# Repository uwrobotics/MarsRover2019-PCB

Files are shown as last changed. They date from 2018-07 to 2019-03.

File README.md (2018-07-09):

# MarsRover2019-PCB
Contains schematics and PCB designs

Conflict Resolution
If you're updating a library or any binary file, and git tells you there is a conflict, please follow the following steps to resolve it:
1. Copy your local version somewhere else (ex. desktop).
2. Undo your changes.
3. Pull all the changes from the repository, overwriting your local copy.
4. Make your changes in the updated version of the file.
5. Commit and push your changes.

If you made a lot of changes, or you suspect someone else is working on the same file as you at the same time, then you can check the change log on github.com, the app, or the terminal (git log) to see who made the most recent changes to the file.

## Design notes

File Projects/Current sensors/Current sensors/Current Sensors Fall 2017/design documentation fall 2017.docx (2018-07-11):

Current Sensor Boards Fall 2017 Design

Overview:

Boards are set up for 3v3 supply voltage.

Sensors are bidirectional and normally output 2.5V <Vout < 4.5V on their respective ranges (20A or 30A). But since a 3v3 supply is used the range is 1.65 <Vout< 2.97 for the full 0-20A range or 0-30A range. For the 5A board, a 20A sensor is being used so the range is 1.65<Vout< 1.98. This voltage range is being mapped onto as close to [0,3.3] as possible to get maximum resolution.

Using a 20A hall-effect sensor to sense current both on 20A and 5A range. Using a 30A hall-effect sensor to sense current on a 30A range. These boards have been tested. Resistor values and current vs voltage from op-amp data is contained in the “20A and 30A board new resistors oct 31 3v3” document.

In progress:

As of November 11 2017:

ADCs have not been ordered. 100A board has not been tested.

The ADCs originally planned for do not have selectable I2C addresses. This is an issue because 6 boards are needed for motors, 1 board for the battery, and one board for the end-effector. To address this problem there are 5 courses of action that can be taken (2, 4 and 5 are most promising because we can buy $1.2 single address ADCs)

1. Purchase eight 5-7$ ADCs with 3 address pins, respin boards
2. Purchase ADA fruit i2c expander break-out (MUX) and run clock and data lines to the break-out then a single SDA and SCL to the arb board
  a. Need a good way of connecting the lines to the breakout
    i. pin headers and solder wires and use wire-wire connectors?
3. Purchase eight 4$ ADCs with 4 selectable addresses and use a transistor to multiplex
4. Buy a $0.60 8:1 multiplexer IC and incorporate it into the arm board. This would mean that connectors would be needed for at least 6 clock and 6 data lines on the actual arm board.
5. Make a separate board for a multiplexer IC and the necessary connectors. Has the benefit of not having too many connectors on the actual arm board and also not having to elaborately find a way to get connectors on the adafruit break-out.

Robert Toyonaga fall 2017

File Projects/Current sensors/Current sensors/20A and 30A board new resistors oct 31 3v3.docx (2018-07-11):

Current | Voltage from op amp (1) | (2) | (3)
0 | 2.36 | 2.406 | 3.278
0.5 | 2.33 | 2.371 | 3.207
1 | 2.30 | 2.340 | 3.138
1.5 | 2.29 | 2.321 | 3.068
2 | 2.28 | 2.310 | 2.999
2.5 | 2.27 | 2.305 | 2.929
3 | | 2.302 | 2.859
3.5 | | | 2.790
4 | | | 2.720
4.5 | | | 2.650
5 | | | 2.581

3v3 20A board

After trial 2. I re-soldered on the op amp. Realized one pad needed more solder. Worked fine afterwards.

3v3 30A board

Current

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
Current | Voltage from op-amp
0 | 3.207
0.5 | 3.161
1 | 3.116
1.5 | 3.071
2 | 3.026
2.5 | 2.981
3 | 2.935
3.5 | 2.890
4 | 2.844
4.5 | 2.797
5 | 2.752

Had issues getting power supply leads to work. Tested with multimeter got 1<r<1Mohm

Make sure banana plugs are in securely sometimes I had to wiggle them in.

Current | Voltage from op-amp
0 | 3.207
0.5 | 3.161
1 | 3.116
1.5 | 3.071
2 | 3.026
2.5 | 2.981
3 | 2.935
3.5 | 2.890
4 | 2.844
4.5 | 2.797
5 | 2.752

3v3 5A

Current | Voltage from op-amp | R68= 39 R21 = 4.7
0 | 3.298 | 3.228
0.5 | 3.195 | 2.946
1 | 2.882 | 2.684
1.5 | 2.569 | 2.422
2 | 2.255 | 2.162
2.5 | 1.948 | 1.903
3 | 1.644 | 1.643
3.5 | 1.334 | 1.385
4 | 1.025 | 1.126
4.5 | 0.714 | 0.865
5 | 0.380 | 0.606

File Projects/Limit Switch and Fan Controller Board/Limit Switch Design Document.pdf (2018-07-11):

# Limit Switch Board Document

## 1 Introduction

This brief document provides a general overview of the Limit Switch Board (or Limits Board), designed for the University of Waterloo Robotics Team (Mars Rover 2018) by Josh Rubin. The schematic and layout for this board can be found on the UW Robotics GrabCad, or the reader can contact the designer to obtain the files if necessary. The reader can contact the board designer at josh.rubin@edu.uwaterloo.ca.

The board serves two major purposes on the UW Mars Rover: it acts as a hardware solution to monitor and control the mechanical limits of the rover’s arm, and to automatically control a fan based on the ambient temperature.

## 2 The Board

The board consists of two major circuits; the limit switch combinational logic, and the temperature dependant fan controller. Each of these circuits will now be discussed in further detail.

### 2.1 Limit Switch Combinational Logic

This section of the board deals with handling the mechanical limits of the rover’s arm. At a high level, the circuit cuts the PWM that is delivered to a motor controller when a limit switch has been triggered and the microcontroller is still supplying the direction signal in the direction that is no longer physically allowed. If this is not the case, the circuit passes PWM to to a motor controller. The circuit does not simply break the PWM indefinitely. If the opposite direction is provided by the controller, the PWM signal will be allowed to pass again, and once the arm reaches a location where the limit switch is no longer closed, the circuit will go back to its original state. The circuit’s operation is clearly explained by an example in Section 2.1.1.

The circuit for 1 motor with bidirectional limiting (mechanical limits on two directions of motion; say, arm moving right and arm moving left) consists of 2 Single Pole Double Throw (SPDT) limit switches, a 2 input XOR gate, and a 2:1 multiplexer (MUX), and connections to HIGH (3.3V), LOW (GND) and associated pull-up and pull-down resistors.

Figure 1 below illustrates a high level (block diagram) of the circuit. The box on the left represents the microcontroller (located on the Arm Board) providing the direction and PWM signals to the motors, the middle block is the combinational logic, and the right block represents the output direction and PWM being fed to the motor drivers.

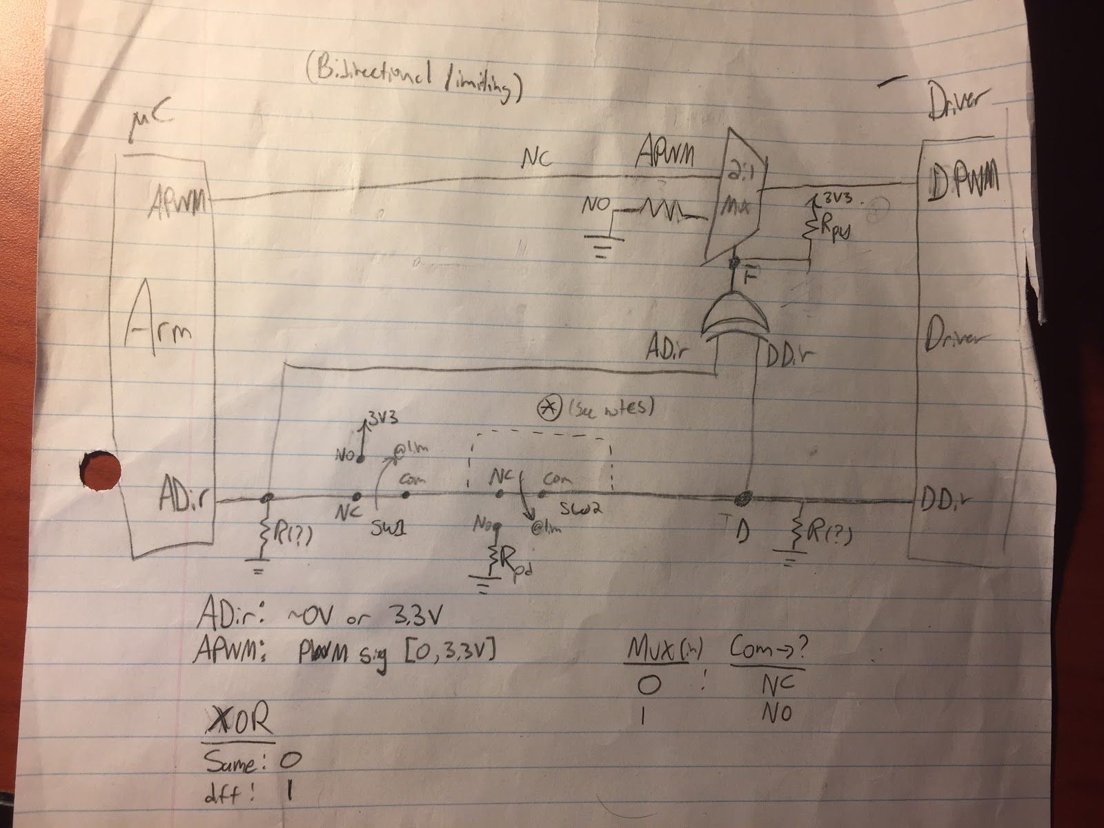
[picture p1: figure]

Figure 1. A block diagram of the limit switch combinational logic.

The operation of the circuit is best described through the use of an example.

2.1.1 Example of Operation
The limit switches are connected so that the direction input is the same as the direction output when a limit has not been reached (ADir = DDir). If one of the limits is reached, the limit switch then switches to the NO position, which is tied to either HIGH or LOW. Since the direction signal is either HIGH (defined as RIGHT for example) or LOW (defined as LEFT for example), this essentially asserts a direction on the motor controller. That is, when a limit switch is triggered, the circuit asserts the opposite direction (i.e., the direction the arm is allowed to move in) on the motor. The next paragraph discusses the PWM, which controls whether or not the motor is moving.

The XOR logic (LOW if the inputs are the same, HIGH if they are different) outputs the digital HIGH/LOW input of the selector on the MUX. If the two direction signals are the same, then the PWM signal will be selected by the MUX (NC signal). If the direction signals are different as is the case when a limit switch has been hit, GND (0 PWM) will be selected by the MUX. That means that when a limit switch has been triggered, the circuit will disable the PWM, and thus stop the motor from moving. The next paragraph discusses how the motor can move in the opposite direction again after a limit has been reached.

The circuit does not prevent the motor from moving indefinitely. If the microcontroller provides the same direction as the one being asserted by the limit switch (that is, the direction of valid motion), then the two direction inputs become the same and thus the XOR logic will ensure that PWM is selected. The reason this is possible is because the ADir and DDir line (seen in Figure
1) is essentially broken into two when a limit is reached. Thus, when a limit is reached, ADir and DDir become different lines, and are therefore independent. This is one of the reasons the logic works in the first place. Once the arm moves such that the limit switch is no longer closed, the circuit goes back to its original state. This logic therefore prevents the motor from being stuck indefinitely.

2.1.2 Notes
1. Shorting one of the limit switches in the circuit causes the limiting to become unidirectional (the operation is the same, except only one direction can be tracked and asserted).
2. The “R(?)” pull-down resistors in Figure 1 are implemented in the final design as pull-down resistors to ensure default logic values at the XOR gates.
3. Additionally, the pull-up resistor (versus pull-down) are used between the XOR and MUX since the sourced XOR uses an Open Collector Output.
4. The D and F markers on Figure 1 (near DDir and the output of the XOR gate) are two signals that are provided to the board’s microcontroller to indicate whether or not a limit has been reached (F) and which direction is currently being asserted by the circuit (D). Note that F could possibly be LOW (not asserted) even if one of the limits is switched. This would only be for the brief period of time between when the motor is moving in the correct direction but the limit switch is still triggered. That being said, if the limit switch is still activated and the controller again provides the invalid direction, the circuit will again cut the PWM since the XOR output will become HIGH once again. This edge case should not impact the operation or correctness of the monitoring.

2.1.3 Sourced Logic Components
2:1 MUX: http://www.ti.com/lit/ds/symlink/ts3a24159.pdf
XOR: http://www.ti.com/lit/ds/symlink/sn74lvc2g86.pdf

### 2.2 Fan Controller

The fan circuit uses the Microchip TC648 Fan Controller. This controller provides a PWM signal to control the speed of a fan depending on the output from a simple temperature sensor circuit.

Depending on the choice of thermistor and resistor values in the temperature circuit, the designer can adjust the temperature range in which the fan will operate, and that PWM will be supplied to the fan within that range. For example, in the originally designed circuit for this board, the fan will run at 50% PWM at 30 degrees, 100% PWM above 50 degrees, and have a roughly linear increase in PWM over that temperature range. The fan will also automatically shut off when the temperature is below 30 degrees (based on the output of a simple voltage divider circuit).

The circuit is essentially the same as the one shown in the device datasheet. The datasheet can be found here: http://ww1.microchip.com/downloads/en/DeviceDoc/21448D.pdf.

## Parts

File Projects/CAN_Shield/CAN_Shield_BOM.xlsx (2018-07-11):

CAN Shield BOM
Part | Quantity | Description | Link | Cost
CAN Transceiver | 1 | TJA1051T/3.118 | https://www.digikey.com/product-detail/en/nxp-usa-inc/TJA1051T-3118/568-8684-1-ND/2803570 | 1.36
Resistor | 2 | 120Ohm SMD 0805 | https://www.digikey.ca/product-detail/en/stackpole-electronics-inc/RMCF0805JT120R/RMCF0805JT120RCT-ND/1942540 | 0.28
Header Pin | 6 | Link gives 3 header pins per unit | https://www.digikey.ca/product-detail/en/wurth-electronics-inc/61300311121/732-5316-ND/4846825 | 0.34
JST Connector | 2 | 3 pin | Not sure where we sourced them last time
 |  |  |  | 1.98

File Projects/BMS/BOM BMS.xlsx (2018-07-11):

quantity | digikey part number | customer reference
1 | DMP2035U-7DICT-ND | (BMS) p chan mosfet
4 | SDM2U40CSP-7BDICT-ND | (BMS) diodes
1 | RR08P8.2KDTR-ND | 8.2k resistors
1 | RR08P2.7KDTR-ND | 2.7k resistors
1 | WM17469-ND | ribbon

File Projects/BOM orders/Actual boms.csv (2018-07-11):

Index | Quantity | Part Number | Manufacturer Part Number | Description | Customer Reference | Backorder | Unit Price | Extended Price
1 | 30 | 490-4781-1-ND | GCM188R72A103KA37D | CAP CER 10000PF 100V X7R 0603 | 10NF | 0 | 0.06800 | $2.04
2 | 30 | 490-9654-1-ND | GRM188R61E104KA01D | CAP CER 0.1UF 25V X5R 0603 | 0.1 UF | 0 | 0.13600 | $4.08
3 | 30 | 490-3298-1-ND | GRM188R60G106ME47D | CAP CER 10UF 4V X5R 0603 | 10UF | 0 | 0.17300 | $5.19
4 | 30 | 478-1215-1-ND | 06035C102KAT2A | CAP CER 1000PF 50V X7R 0603 | 1NF | 0 | 0.07800 | $2.34
5 | 30 | 455-1819-ND | B04B-PASK(LF)(SN) | CONN HEADER PA 4POS TOP 2MM TIN | PWR AND I2C CONN 180 TH | 0 | 0.44400 | $13.32
6 | 30 | 455-1488-ND | PAP-04V-S | CONN HOUSING PA 4POS 2MM WHITE | HOUSINGS PWR AND I2C | 0 | 0.16640 | $4.99
7 | 60 | 455-1325-1-ND | SPHD-001T-P0.5 | CONN TERM PHD CRIMP 22-26AWG TIN | CRIMPS PWR AND I2C | 0 | 0.04980 | $2.99
8 | 10 | MCP6001T-I/OTCT-ND | MCP6001T-I/OT | IC OPAMP GP 1MHZ RRO SOT23-5 | OP AMP | 0 | 0.37000 | $3.70
9 | 30 | RNCF0805DTE10K0CT-ND | RNCF0805DTE10K0 | RES 10K OHM 0.5% 1/8W 0805 | RES SMD 10K OHM 0.5% 1/8W 0805 | 0 | 0.20800 | $6.24
10 | 30 | P18KDACT-ND | ERA-6AEB183V | RES SMD 18K OHM 0.1% 1/8W 0805 | RES SMD 18K OHM 0.1% 1/8W 0805 | 0 | 0.44800 | $13.44
11 | 30 | P22KDACT-ND | ERA-6AEB223V | RES SMD 22K OHM 0.1% 1/8W 0805 | RES SMD 22K OHM 0.1% 1/8W 0805 | 0 | 0.44800 | $13.44
12 | 10 | 620-1191-1-ND | ACS712ELCTR-30A-T | SENSOR CURRENT HALL 30A AC/DC | 30A SENSOR | 0 | 5.85300 | $58.53
13 | 10 | ADC081C021CIMM/NOPBCT-ND | ADC081C021CIMM/NOPB | IC ADC 8BIT I2C 188KSPS 8VSSOP | IC ADC 8BIT I2C 188KSPS 8VSSOP | 0 | 2.20900 | $22.09
14 | 10 | ED2677-ND | OSTT7022150 | TERMINAL BLOCK 9.52MM 2POS PCB | SCREW TERMS | 0 | 1.48000 | $14.80
15 | 20 | 445-8018-1-ND | C1005X5R1E334K050BB | CAP CER 0.33UF 25V X5R 0402 | 0.33UF | 0 | 0.18500 | $3.70
16 | 20 | 490-3298-1-ND | GRM188R60G106ME47D | CAP CER 10UF 4V X5R 0603 | 10UF | 0 | 0.17300 | $3.46
17 | 40 | 490-3117-1-ND | GJM1555C1H150JB01D | CAP CER 15PF 50V C0G/NP0 0402 | 15 PF | 0 | 0.22000 | $8.80
18 | 20 | 311-1372-1-ND | CC0603ZRY5V7BB105 | CAP CER 1UF 16V Y5V 0603 | 1UF | 0 | 0.08600 | $1.72
19 | 30 | 455-1578-1-ND | BM02B-GHS-TBT(LF)(SN)(N) | CONN HEADER GH TOP 2POS 1.25MM | GH 2 | 0 | 0.56400 | $16.92
20 | 20 | 455-1579-1-ND | BM03B-GHS-TBT(LF)(SN)(N) | CONN HEADER GH TOP 3POS 1.25MM | GH 3 | 0 | 0.62800 | $12.56
21 | 30 | 455-1580-1-ND | BM04B-GHS-TBT(LF)(SN)(N) | CONN HEADER GH TOP 4POS 1.25MM | GH4 | 0 | 0.57500 | $17.25
22 | 30 | 455-1581-1-ND | BM05B-GHS-TBT(LF)(SN)(N) | CONN HEADER GH TOP 5POS 1.25MM | GH 5 | 0 | 0.60100 | $18.03
23 | 10 | 1253-1730-1-ND | CX2520DB32000D0GPSC1 | CRYSTAL 32.0000MHZ 8PF SMD | CRYSTAL | 0 | 0.88100 | $8.81
24 | 10 | MC33269DT-3.3GOS-ND | MC33269DT-3.3G | IC REG LINEAR 3.3V 800MA DPAK-3 | LDO | 0 | 0.95200 | $9.52
25 | 7 | LTC2875HS8#PBF-ND | LTC2875HS8#PBF | IC TXRX CAN 4MBPS 8SO | TRANCEIVER | 7 | 6.39000 | $44.73
26 | 20 | 1642-1324-1-ND | LS75C4D-T | SWITCH TACT SPST-NO 0.02A 12V | BUTTON PWR | 0 | 0.55700 | $11.14
27 | 20 | CKN10777CT-ND | KXT 311 LHS | SWITCH TACTILE SPST-NO 0.02A 15V | BUTTON SIGNAL | 0 | 0.35400 | $7.08
28 | 20 | 311-120GRCT-ND | RC0603JR-07120RL | RES SMD 120 OHM 5% 1/10W 0603 | 120 R | 0 | 0.01600 | $0.32
29 | 10 | 497-15167-ND | STM32F091RCT6 | IC MCU 32BIT 256KB FLASH 64LQFP | STM32F091RC | 0 | 5.94900 | $59.49
30 | 10 | 1727-1306-1-ND | PESD1CAN-UX | TVS DIODE 24V 50V SOT323-3 | CAN DIODE | 0 | 0.43200 | $4.32
31 | 15 | PCE4549CT-ND | EEE-FPV100UAR | CAP ALUM 10UF 20% 35V SMD | 10 UF POLARIZED | 0 | 0.50400 | $7.56
32 | 2 | VEML7700CT-ND | VEML7700-TR | IC AMBIENT LIGHT SENSOR I2C SMT | LIGHT SENSOR | 0 | 2.88000 | $5.76
33 | 10 | 455-1833-ND | B03B-PASK-1(LF)(SN) | CONN HEADER PA 3POS TOP W/BOSS | PA 3 | 0 | 0.37200 | $3.72
34 | 5 | DMP2035U-7DICT-ND | DMP2035U-7 | MOSFET P-CH 20V 3.6A SOT-23 | (BMS) P CHAN MOSFET | 0 | 0.78000 | $3.90
35 | 10 | SDM2U40CSP-7BDICT-ND | SDM2U40CSP-7B | DIODE SCHOTTKY 40V 2A X3-WLB1608 | (BMS) DIODES | 0 | 0.48200 | $4.82
36 | 10 | P8.2KDBCT-ND | ERA-3AEB822V | RES SMD 8.2K OHM 0.1% 1/10W 0603 | 8.2K RESISTORS | 0 | 0.44500 | $4.45
37 | 10 | RR08P2.7KDCT-ND | RR0816P-272-D | RES SMD 2.7K OHM 0.5% 1/16W 0603 | 2.7K RESISTORS | 0 | 0.14500 | $1.45
38 | 4 | WM17469-ND | 0878311420 | CONN HEADER 14POS 2MM VERT GOLD | RIBBON | 0 | 1.91000 | $7.64
39 | 1 | 455-1602-ND | GHR-12V-S | CONN GH HOUSING 12POS 1.25MM | 12 GH HOUSE | 0 | 0.28000 | $0.28
40 | 30 | 455-1594-ND | GHR-04V-S | CONN GH HOUSING 4POS 1.25MM | 4 GH HOUSE | 0 | 0.12920 | $3.88
41 | 10 | 455-1486-ND | PAP-02V-S | CONN HOUSING PA 2POS 2MM WHITE | 2 PA HOUSE | 0 | 0.19600 | $1.96
42 | 30 | 455-1595-ND | GHR-05V-S | CONN GH HOUSING 5POS 1.25MM | 5 GH HOUSE | 0 | 0.19040 | $5.71
43 | 50 | 455-1313-1-ND | SPHD-002T-P0.5 | CONN TERM PHD CRIMP 24-28AWG TIN | PA CRIMP | 0 | 0.04980 | $2.49
44 | 40 | 1276-1045-1-ND | CL10A475KQ8NNNC | CAP CER 4.7UF 6.3V X5R 0603 | 4.7 UF | 0 | 0.09600 | $3.84
45 | 20 | 475-1410-1-ND | LG R971-KN-1 | LED GREEN DIFFUSED 0805 SMD | GRN | 0 | 0.33400 | $6.68
46 | 20 | 475-1278-1-ND | LS R976-NR-1 | LED RED DIFFUSED 0805 SMD | RED | 0 | 0.35200 | $7.04
47 | 20 | 475-2560-1-ND | LY R976-PS-36 | LED YELLOW DIFFUSED 0805 SMD | YELLOW | 0 | 0.35200 | $7.04
48 | 40 | MCT0603-0.0-ZZCT-ND | MCT06030Z0000ZP500 | RES SMD 0 OHM JUMPER 1/8W 0603 | 0R | 0 | 0.25840 | $10.34
49 | 50 | RNCF0805DTE10K0CT-ND | RNCF0805DTE10K0 | RES 10K OHM 0.5% 1/8W 0805 | RES SMD 10K OHM 0.5% 1/8W 0805 | 0 | 0.20800 | $10.40
50 | 40 | 311-4.7KGRCT-ND | RC0603JR-074K7L | RES SMD 4.7K OHM 5% 1/10W 0603 | 4.7 K | 0 | 0.01600 | $0.64
51 | 20 | 455-1593-ND | GHR-03V-S | CONN GH HOUSING 3POS 1.25MM | 3 GH HOUSE | 0 | 0.16600 | $3.32
52 | 20 | 455-1487-ND | PAP-03V-S | CONN HOUSING PA 3POS 2MM WHITE | 3 PA HOUSE | 0 | 0.20500 | $4.10
 |  |  |  |  |  |  | Subtotal | $502.06

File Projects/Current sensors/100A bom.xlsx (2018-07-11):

quant | digikey pn | cust ref | board | link
1 | 490-4781-1-ND | 10nF | 100A
2 | 587-1245-1-ND | 0.1 uF | 100A
2 | 490-3298-1-ND | 10uf | 100A
1 | 478-1215-1-ND | 1nf | 100A
3 | 455-1819-ND | pwr and i2c conn 180 th | 100A
3 | 455-1488-ND | housings pwr and i2c | 100A
6 | 455-1325-1-ND | crimps pwr and i2c | 100A
1 | MCP6001T-I/OTCT-ND | op amp | 100A
2 | RNCF0805DTE10K0CT-ND | RES SMD 10K OHM 0.5% 1/8W 0805 | 100A
1 | P18KDACT-ND | RES SMD 18K OHM 0.1% 1/8W 0805 | 100A
1 | P22KDACT-ND | RES SMD 22K OHM 0.1% 1/8W 0805 | 100A
1 | 620-1465-5-ND | 100A sensor | 100A
1 | ADC081C021CIMM/NOPBCT-ND | IC ADC 8BIT I2C 188KSPS 8VSSOP | 100A

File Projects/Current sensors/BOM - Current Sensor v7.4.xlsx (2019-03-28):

RefDes | Value | Name | Part | Number of Pins | Pattern | Manufacturer | Manufacturer Part Number | Quantity | DigiKey Part Numbers | Datasheet
C1 | 1 nF | CAP_0805 | Part 1 | 2 | CAP_0805 | KEMET | C0402C102K5RACTU | 1 | 399-1032-2-ND (https://www.digikey.ca/product-detail/en/kemet/C0402C102K5RACTU/399-1032-2-ND/411034) | https://content.kemet.com/datasheets/KEM_C1002_X7R_SMD.pdf
C2 | 0.1 uF | CAP_0805 | Part 1 | 2 | CAP_0805 | KEMET | C0402C102K5RACTU | 1 | 399-1032-2-ND (https://www.digikey.ca/product-detail/en/kemet/C0402C102K5RACTU/399-1032-2-ND/411034) | https://content.kemet.com/datasheets/KEM_C1002_X7R_SMD.pdf
C3 | 10 uF | CAP_0805 | Part 1 | 2 | CAP_0805 | KEMET | C0402C102K5RACTU | 1 | 399-1032-2-ND (https://www.digikey.ca/product-detail/en/kemet/C0402C102K5RACTU/399-1032-2-ND/411034) | https://content.kemet.com/datasheets/KEM_C1002_X7R_SMD.pdf
C13 | 1 nF | CAP_0805 | Part 1 | 2 | CAP_0805 | KEMET | C0402C102K5RACTU | 1 | 399-1032-2-ND | https://content.kemet.com/datasheets/KEM_C1002_X7R_SMD.pdf
C14 | 10 uF | CAP_0805 | Part 1 | 2 | CAP_0805 | KEMET | C0402C102K5RACTU | 1 | 399-1032-2-ND | https://content.kemet.com/datasheets/KEM_C1002_X7R_SMD.pdf
C15 | 0.1 uF | CAP_0805 | Part 1 | 2 | CAP_0805 | KEMET | C0402C102K5RACTU | 1 | 399-1032-2-ND | https://content.kemet.com/datasheets/KEM_C1002_X7R_SMD.pdf
J1 |  | CON_2M_PH_TOP_SMT | Part 1 | 2 | JST-B2B-SM4-TB | Sponsored by JST | Sponsored by JST | 1 | Sponsored by JST | http://www.jst-mfg.com/product/pdf/eng/ePH.pdf
J4 |  | CON_4M_PH_TOP_SMT | Part 1 | 4 | JST-B4B-SM4-TB | Sponsored by JST | Sponsored by JST | 1 | Sponsored by JST | http://www.jst-mfg.com/product/pdf/eng/ePH.pdf
OPAMP |  | MCP6001(op amp) | Part 1 | 5 | MCP6001 | MICROCHIP | MCP6001RT-E/OT | 1 | MCP6001RT-E/OTCT-ND | http://ww1.microchip.com/downloads/en/DeviceDoc/21733j.pdf
R1 | 10K | RES | Part 1 | 2 | RES_0603 | Stackpole Electronics | RMCF0201FT10K0 | 1 | RMCF0201FT10K0TR-ND (https://www.digikey.com/product-detail/en/stackpole-electronics-inc/RMCF0201FT10K0/RMCF0201FT10K0TR-ND/1714990) | https://www.seielect.com/catalog/sei-rmcf_rmcp.pdf
R2 | 10K | RES | Part 1 | 2 | RES_0603 | Stackpole Electronics | RMCF0201FT10K0 | 1 | RMCF0201FT10K0TR-ND (https://www.digikey.com/product-detail/en/stackpole-electronics-inc/RMCF0201FT10K0/RMCF0201FT10K0TR-ND/1714990) | https://www.seielect.com/catalog/sei-rmcf_rmcp.pdf
R8 | 10K | RES | Part 1 | 2 | RES_0603 | Stackpole Electronics | RMCF0201FT10K0 | 1 | RMCF0201FT10K0TR-ND | https://www.seielect.com/catalog/sei-rmcf_rmcp.pdf
R9 | 10K | RES | Part 1 | 2 | RES_0603 | Stackpole Electronics | RMCF0201FT10K0 | 1 | RMCF0201FT10K0TR-ND | https://www.seielect.com/catalog/sei-rmcf_rmcp.pdf
R24 | 10K | RES_0805 | Part 1 | 2 | RES_0805 | Stackpole Electronics | RMCF0201FT10K0 | 1 | RMCF0201FT10K0TR-ND (https://www.digikey.com/product-detail/en/stackpole-electronics-inc/RMCF0201FT10K0/RMCF0201FT10K0TR-ND/1714990) | https://www.seielect.com/catalog/sei-rmcf_rmcp.pdf
R25 | 18K | RES_0805 | Part 1 | 2 | RES_0805 | Panasonic | ERA-3AEB183V | 1 | P18KDBTR-ND | https://industrial.panasonic.com/cdbs/www-data/pdf/RDM0000/AOA0000C307.pdf
R26 | 10K | RES_0805 | Part 1 | 2 | RES_0805 | Stackpole Electronics | RMCF0201FT10K0 | 1 | RMCF0201FT10K0TR-ND (https://www.digikey.com/product-detail/en/stackpole-electronics-inc/RMCF0201FT10K0/RMCF0201FT10K0TR-ND/1714990) | https://www.seielect.com/catalog/sei-rmcf_rmcp.pdf
R27 | 22K | RES_0805 | Part 1 | 2 | RES_0805 | Panasonic | ERA-3AEB223V | 1 | P22KDBTR-ND | https://industrial.panasonic.com/cdbs/www-data/pdf/RDM0000/AOA0000C307.pdf
sensor | 100A | ACS759 | Part 1 | 5 | ACS759 | Allegro Microsystems | ACS759LCB-100B-PFF-T | 1 | 620-1465-5-ND | www.allegromicro.com/~/media/Files/Datasheets/ACS759-Datasheet.ashx
U1 |  | ADC081C027 | Part 1 | 8 | IC ADC 8BIT I2C 188KSPS 8VSSOP | Texas Instruments | ADC081C027CIMKX/NOPB | 1 | ADC081C027CIMKX/NOPBTR-ND | http://www.ti.com/lit/ds/symlink/adc081c021.pdf
 |  |  |  | 52 |  |  |  | 19

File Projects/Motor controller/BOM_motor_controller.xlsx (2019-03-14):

Good? | Quantity | Name | Manufacturer | MPN | Price/unit | Total price | Digikey Link
Y | 3 | CAP_1uF_0603 | Yageo | CC0603ZRY5V7BB105 | 0.14 | 0.42 | https://www.digikey.ca/product-detail/en/yageo/CC0603ZRY5V7BB105/311-1372-1-ND/2103156
Y | 2 | CAP_0.1uF_0603 | Taiyo Yuden | GMK107B7104KAHT | 0.2 | 0.4 | https://www.digikey.ca/product-detail/en/taiyo-yuden/GMK107B7104KAHT/587-3354-1-ND/4157241
Y? | 1 | CAP_1000uF_POL | Illinois Capacitor | 108CKE050M | 1.23 | 1.23 | https://www.digikey.ca/products/en?keywords=108CKE050M
Y | 1 | CAP_10uF_2917 | Vishay Sprague | 293D106X0035D2TE3 | 0.9 | 0.9 | https://www.digikey.ca/product-detail/en/vishay-sprague/293D106X0035D2TE3/718-1046-1-ND/1559540
N | 1 | CAP_100nF_0603 | Yageo | CC0603KRX7R7BB104 | 0.14 | 0.14 | https://www.digikey.ca/product-detail/en/yageo/CC0603KRX7R7BB104/311-1088-1-ND/302998
N | 1 | BAS16GW | Nexperia | BAS16GW | 0.14 | 0.14 | https://www.digikey.ca/product-detail/en/nexperia-usa-inc/BAS16GWJ/1727-7320-1-ND/7390571
Y | 1 | DIO_LED_G | OSRAM | LG R971-KN-1 | 0.45 | 0.45 | https://www.digikey.ca/product-detail/en/osram-opto-semiconductors-inc/LG-R971-KN-1/475-1410-1-ND/1802598
Y | 1 | CON_3M_TH_180 | JST | JST-B03B-PASK | 0.38 | 0.38 | https://www.digikey.ca/product-detail/en/jst-sales-america-inc/B03B-PASK-1-LF-SN/455-1833-ND/926739
Y | 1 | Female for CON_3M_TH_180 | JST | PAP-03V-S | 0.22 | 0.22 | https://www.digikey.ca/product-detail/en/jst-sales-america-inc/PAP-03V-S/455-1487-ND/759975
Y | 2 | CON_2M_30A | On Shore Technology Inc | OSTYK51102030 | 1.37 | 2.74 | https://www.digikey.ca/product-detail/en/on-shore-technology-inc/OSTYK51102030/ED2953-ND/1588818
Y | 5 | NMOS_40V_75A | Nexperia | BUK765R3-40E | 1.46 | 7.3 | https://www.digikey.ca/product-detail/en/nexperia-usa-inc/BUK765R3-40E118/1727-7255-1-ND/3672520
Y? | 3 | NPN_40V_100mA | Micro Commercial Co | MMBT3904-TP | 0.14 | 0.42 | https://www.digikey.ca/product-detail/en/micro-commercial-co/MMBT3904-TP/MMBT3904TPMSCT-ND/717395
Y? | 1 | RES_43k_0603 | Yageo | RC0603JR-0743KL | 0.15 | 0.15 | https://www.digikey.ca/product-detail/en/yageo/RC0603JR-0743KL/311-43KGRCT-ND/729737
Y | 1 | RES_100R_0603 | Yageo | RC0603FR-07100RL | 0.15 | 0.15 | https://www.digikey.ca/product-detail/en/yageo/RC0603FR-07100RL/311-100HRCT-ND/729835
Y | 1 | RES_698k_0603 | Yageo | RC0603FR-07698KL | 0.15 | 0.15 | https://www.digikey.ca/product-detail/en/yageo/RC0603FR-07698KL/311-698KHRCT-ND/730309
Y? | 6 | RES_10K_0603 | Yageo | RC0603JR-0710KL | 0.15 | 0.9 | https://www.digikey.ca/product-detail/en/yageo/RC0603JR-0710KL/311-10KGRCT-ND/729647
Y | 2 | RES_150k_0603 | Yageo | RC0603JR-07150KL | 0.15 | 0.3 | https://www.digikey.ca/product-detail/en/yageo/RC0603JR-07150KL/311-150KGRCT-ND/729662
 | 2 | PUSHBUTTON_TACTILE | C&K | RS-282G05A3-SM RT | 1.15 | 2.3 | https://www.digikey.ca/product-detail/en/c-k/RS-282G05A3-SM-RT/CKN10384CT-ND/2747203
Y | 1 | DRV8701E | Texas Instruments | DRV8701ERGET | 4.12 | 4.12 | https://www.digikey.ca/product-detail/en/texas-instruments/DRV8701ERGET/296-42155-1-ND/5299196
Y | 1 | XOR_1 | ON Semiconductor | NC7SV86P5XCT-ND | 0.55 | 0.55 | https://www.digikey.ca/products/en?keywords=NC7SV86P5XCT-ND
Y | 1 | OSCILLATOR_2kHz | Microchip Technology | DSC6083CI2A-002K000 | 1.35 | 1.35 | https://www.digikey.ca/product-detail/en/microchip-technology/DSC6083CI2A-002K000/DSC6083CI2A-002K000-ND/6244496
 |  |  |  |  | Total | 23.13
 | 2 | SN74AHC1G02DBVT | Texas Instruments | SN74AHC1G02DBVT |  |  | https://www.digikey.ca/product-detail/en/texas-instruments/SN74AHC1G02DBVT/296-49867-1-ND/9462743
 | 2 | 74LVC1G3157GW,125 | Nexperia | 74LVC1G3157GW,125 |  |  | https://www.digikey.ca/product-detail/en/nexperia-usa-inc/74LVC1G3157GW125/1727-6073-1-ND/2753909

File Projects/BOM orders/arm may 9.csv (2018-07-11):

# | Quantity | MPN | Name | Value
17 | 1 | GRM188R71C334KA01D | CAP_0.33uF_0603 | 0.33uF
7 | 1 | CC0603KRX7R7BB104 | CAP_100nF_0603 | 100nF
8 | 1 | CC0603KRX7R7BB104 | CAP_100nF_0603 | 100nF
9 | 1 | CC0603KRX7R7BB104 | CAP_100nF_0603 | 100nF
10 | 1 | CC0603KRX7R7BB104 | CAP_100nF_0603 | 100nF
15 | 1 | CC0603KRX7R7BB104 | CAP_100nF_0603 | 100nF
16 | 1 | CC0603KRX7R7BB104 | CAP_100nF_0603 | 100nF
5 | 1 | CC0402KRX7R6BB103 | CAP_10nF_0603 | 10nF
12 | 1 |  | CAP_10uF_POL | 10uF
13 | 1 | GRM1555C1H150JA01D | CAP_15pF_0402 | 15pF
14 | 1 | GRM1555C1H150JA01D | CAP_15pF_0402 | 15pF
6 | 1 | CC0603ZRY5V7BB105 | CAP_1uF_0603 | 1uF
11 | 1 | CC0603KRX5R5BB475 | CAP_4.7uF_0603 | 4.7uF
18 | 1 | CC0603KRX5R5BB475 | CAP_4.7uF_0603 | 4.7uF
29 | 1 |  | CON _12M_SM_180
44 | 1 |  | CON_2M_SM_180
43 | 1 |  | CON_2M_TH_180
31 | 1 |  | CON_3M_SM_180
32 | 1 |  | CON_3M_SM_180
33 | 1 |  | CON_3M_SM_180
39 | 1 |  | CON_3M_SM_180
41 | 1 |  | CON_3M_SM_180
45 | 1 |  | CON_3M_SM_180
30 | 1 |  | CON_4M_SM_180
36 | 1 |  | CON_4M_SM_180
37 | 1 |  | CON_4M_SM_180
38 | 1 |  | CON_4M_SM_180
34 | 1 |  | CON_5M_SM_180
35 | 1 |  | CON_5M_SM_180
40 | 1 |  | CON_5M_SM_180
42 | 1 |  | CON_5M_SM_180
73 | 1 |  | CRYSTAL | 8MHz
22 | 1 | LG R971-KN-1 | DIO_LED_G | GREEN
23 | 1 | LG R971-KN-1 | DIO_LED_G | GREEN
24 | 1 | LG R971-KN-1 | DIO_LED_G | GREEN
26 | 1 | LS R976-NR-1 | DIO_LED_R | RED
25 | 1 | LY R976-PS-36 | DIO_LED_Y | YELLOW
69 | 1 | MC33269DT-3.3 | LDO_3V3_DPAK
68 | 1 |  | LTC2875 | IC TXRX CAN
64 | 1 | FSM2JSMAA | PUSHBUTTON_PWR
3 | 1 | KXT 311 LHS | PUSHBUTTON_SIGNAL
4 | 1 | KXT 311 LHS | PUSHBUTTON_SIGNAL
59 | 1 | RC0603JR-070RL | RES_0R_0603 | 0R
61 | 1 | RC0603JR-070RL | RES_0R_0603 | 0R
55 | 1 | RC0603FR-07100RL | RES_100R_0603 | 100R
56 | 1 | RC0603FR-07100RL | RES_100R_0603 | 100R
57 | 1 | RC0603FR-07100RL | RES_100R_0603 | 100R
58 | 1 | RC0603FR-07100RL | RES_100R_0603 | 100R
62 | 1 | RC0603FR-07100RL | RES_100R_0603 | 100R
46 | 1 | RC0603JR-0710KL | RES_10K_0603 | 10K
47 | 1 | RC0603JR-0710KL | RES_10K_0603 | 10K
48 | 1 | RC0603JR-0710KL | RES_10K_0603 | 10K
49 | 1 | RC0603JR-0710KL | RES_10K_0603 | 10K
50 | 1 | RC0603JR-0710KL | RES_10K_0603 | 10K
51 | 1 | RC0603JR-0710KL | RES_10K_0603 | 10K
52 | 1 | RC0603JR-0710KL | RES_10K_0603 | 10K
63 | 1 | RC0603JR-0710KL | RES_10K_0603 | 10K
60 | 1 | RC0603JR-07120RL | RES_120R_0603 | 120R
53 | 1 | RC0603JR-074K7L | RES_4.7K_0603 | 4.7K
54 | 1 | RC0603JR-074K7L | RES_4.7K_0603 | 4.7K
67 | 1 |  | STM32F091RC
1 | 1 |  | TESTPOINT
2 | 1 |  | TESTPOINT
19 | 1 |  | TESTPOINT
20 | 1 |  | TESTPOINT
27 | 1 |  | TESTPOINT
28 | 1 |  | TESTPOINT
65 | 1 |  | TESTPOINT
66 | 1 |  | TESTPOINT
70 | 1 |  | TESTPOINT
71 | 1 |  | TESTPOINT
72 | 1 |  | TESTPOINT
21 | 1 | PESD1CAN-UX | TVS_DIODE_CAN
 | 73

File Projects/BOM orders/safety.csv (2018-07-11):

# | Quantity | MPN | Name | Value
1 | 1 |  | TESTPOINT
2 | 1 |  | TESTPOINT
3 | 1 |  | TESTPOINT
4 | 1 |  | JST-B02B-PASK
5 | 1 | RC0603JR-070RL | RES_0R_0603 | 0R
6 | 1 |  | TESTPOINT
7 | 1 |  | JST-B02B-PASK
8 | 1 |  | TESTPOINT
9 | 1 | RC0603JR-070RL | RES_0R_0603 | 0R
10 | 1 |  | JST-B02B-PASK
11 | 1 | RC0603JR-070RL | RES_0R_0603 | 0R
12 | 1 |  | TESTPOINT
13 | 1 |  | JST-B02B-PASK
14 | 1 | KXT 311 LHS | PUSHBUTTON_SIGNAL
15 | 1 | KXT 311 LHS | PUSHBUTTON_SIGNAL
16 | 1 |  | TESTPOINT
17 | 1 |  | TESTPOINT
18 | 1 | GRM1555C1H150JA01D | CAP_15pF_0402 | 15pF
19 | 1 | GRM1555C1H150JA01D | CAP_15pF_0402 | 15pF
20 | 1 | CC0603KRX7R7BB104 | CAP_100nF_0603 | 100nF
21 | 1 | CC0603KRX7R7BB104 | CAP_100nF_0603 | 100nF
22 | 1 | CC0603KRX7R7BB104 | CAP_100nF_0603 | 100nF
23 | 1 | CC0603KRX7R7BB104 | CAP_100nF_0603 | 100nF
24 | 1 | CC0603KRX5R5BB475 | CAP_4.7uF_0603 | 4.7uF
25 | 1 | CC0603KRX7R7BB104 | CAP_100nF_0603 | 100nF
26 | 1 | CC0603KRX5R5BB475 | CAP_4.7uF_0603 | 4.7uF
27 | 1 | CC0402KRX7R6BB103 | CAP_10nF_0603 | 10nF
28 | 1 | CC0603ZRY5V7BB105 | CAP_1uF_0603 | 1uF
29 | 1 | GRM188R71C334KA01D | CAP_0.33uF_0603 | 0.33uF
30 | 1 |  | CAP_10uF_POL | 10uF
31 | 1 | CC0603KRX7R7BB104 | CAP_100nF_0603 | 100nF
32 | 1 | 860020672011 | CAP_22uF_POL | 10uF
33 | 1 | CC0603KRX7R7BB104 | CAP_100nF_0603 | 100nF
34 | 1 | 860020672011 | CAP_22uF_POL | 10uF
35 | 1 | CC0603KRX7R7BB104 | CAP_100nF_0603 | 100nF
36 | 1 |  | TESTPOINT
37 | 1 |  | TESTPOINT
38 | 1 | CC0402KRX7R6BB103 | CAP_10nF_0603 | 10nF
39 | 1 | CC0402KRX7R6BB103 | CAP_10nF_0603 | 10nF
40 | 1 | CC0603ZRY5V7BB105 | CAP_1uF_0603 | 1uF
41 | 1 | CC0603ZRY5V7BB105 | CAP_1uF_0603 | 1uF
42 | 1 |  | DIO_SCHOTTKY
43 | 1 |  | DIO_SCHOTTKY
44 | 1 | LS R976-NR-1 | DIO_LED_R | RED
45 | 1 | LY R976-PS-36 | DIO_LED_Y | YELLOW
46 | 1 | LG R971-KN-1 | DIO_LED_G | GREEN
47 | 1 | PESD1CAN-UX | TVS_DIODE_CAN
48 | 1 | LG R971-KN-1 | DIO_LED_G | GREEN
49 | 1 | LG R971-KN-1 | DIO_LED_G | GREEN
50 | 1 |  | TESTPOINT
51 | 1 |  | TESTPOINT
52 | 1 |  | JST-B02B-PASK
53 | 1 |  | CON_4M_SM_180
54 | 1 |  | CON_4M_SM_180
55 | 1 |  | CON_3M_SM_180
56 | 1 |  | CON_5M_TH_180
57 | 1 |  | CON_4M_SM_180
58 | 1 |  | CON_3M_SM_180
59 | 1 |  | CON_5M_TH_180
60 | 1 |  | CON_3M_TH_180
61 | 1 |  | RES_THERMIS_NTC
62 | 1 |  | MOSFET_ENH_P
63 | 1 |  | MOSFET_ENH_N
64 | 1 |  | MOSFET_ENH_N
65 | 1 | AO3420 | NMOS_20V_6A
66 | 1 | RC0603JR-070RL | RES_0R_0603 | 0R
67 | 1 |  | RES_FIXED | 2.7k
68 | 1 |  | RES_FIXED | 8.2k
69 | 1 | RC0603FR-07100RL | RES_100R_0603 | 100R
70 | 1 | RC0603JR-0710KL | RES_10K_0603 | 10K
71 | 1 | RC0603JR-0710KL | RES_10K_0603 | 10K
72 | 1 | RC0603JR-074K7L | RES_4.7K_0603 | 4.7K
73 | 1 | RC0603JR-074K7L | RES_4.7K_0603 | 4.7K
74 | 1 | RC0603JR-0710KL | RES_10K_0603 | 10K
75 | 1 | RC0603JR-070RL | RES_0R_0603 | 0R
76 | 1 | RC0603FR-07100RL | RES_100R_0603 | 100R
77 | 1 | RC0603FR-07100RL | RES_100R_0603 | 100R
78 | 1 | RC0603JR-07120RL | RES_120R_0603 | 120R
79 | 1 | RC0603FR-07100RL | RES_100R_0603 | 100R
80 | 1 | RC0603FR-07100RL | RES_100R_0603 | 100R
81 | 1 | RC0603JR-0710KL | RES_10K_0603 | 10K
82 | 1 | RC0603JR-0710KL | RES_10K_0603 | 10K
83 | 1 |  | RES_FIXED | 10k
84 | 1 |  | RES_FIXED | 6.8k
85 | 1 |  | RES_FIXED | 6.8k
86 | 1 | RC0603JR-074K7L | RES_4.7K_0603 | 4.7K
87 | 1 | RC0603JR-074K7L | RES_4.7K_0603 | 4.7K
88 | 1 |  | RES_78.5k_0603 | 78.5k
89 | 1 |  | RES_85k_0603 | 85k
90 | 1 |  | RES_30.1k_0603 | 30.1k
91 | 1 |  | RES_20k_0603 | 20k
92 | 1 |  | RES_FIXED | 10k
93 | 1 |  | JST-B02B-PASK
94 | 1 |  | JST-B02B-PASK
95 | 1 |  | JST-B02B-PASK
96 | 1 |  | TESTPOINT
97 | 1 |  | TESTPOINT
98 | 1 |  | TESTPOINT
99 | 1 |  | TESTPOINT
100 | 1 | KXT 311 LHS | PUSHBUTTON_SIGNAL
101 | 1 |  | TESTPOINT
102 | 1 |  | TESTPOINT
103 | 1 |  | TESTPOINT
104 | 1 |  | STM32F091RC
105 | 1 | MC33269DT-3.3 | LDO_3V3_DPAK
106 | 1 |  | LTC2875 | IC TXRX CAN
107 | 1 |  | TC648B_OA
108 | 1 |  | CRYSTAL | 8MHz
 | 108

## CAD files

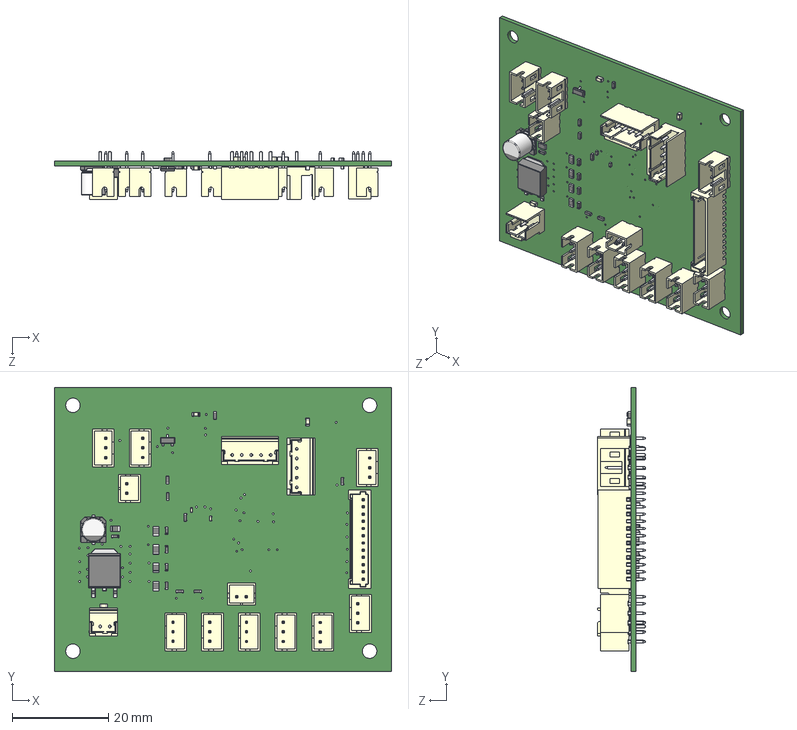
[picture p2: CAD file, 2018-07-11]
Projects/Arm board/armboard1_layout_12PINCONNECTOR.step
70.0 x 59.0 x 10.0 mm
Board
cap_0603 x 10
capae-5.3x5.3h6.1
cap_0402 x 2
sot23
res_0805 x 5
hdr-1x12tz_1.5_sh21x5
hdr-1x2t_2_sh6x5 x 2
hdr-1x3t_2_sh8x5 x 9
hdr-1x5t_2_sh12x6 x 2
hdr-1x2t_2_sh6x6
res_0603 x 18
to252-3(4)_10x6.6x2.28

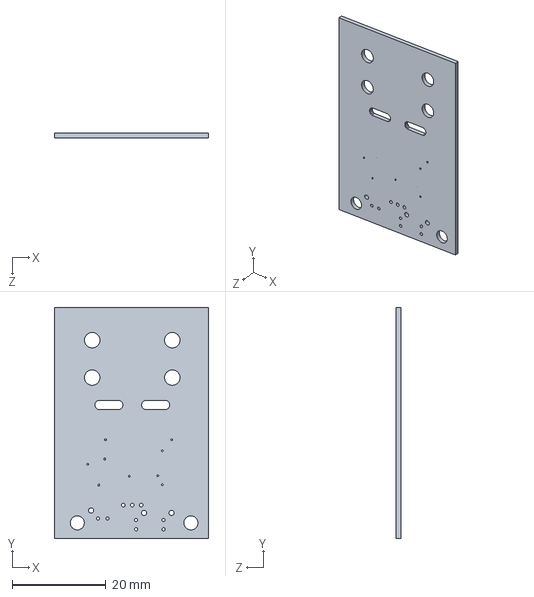
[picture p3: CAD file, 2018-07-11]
Projects/Current sensors/3d model.step
33.0 x 49.4 x 1.00 mm

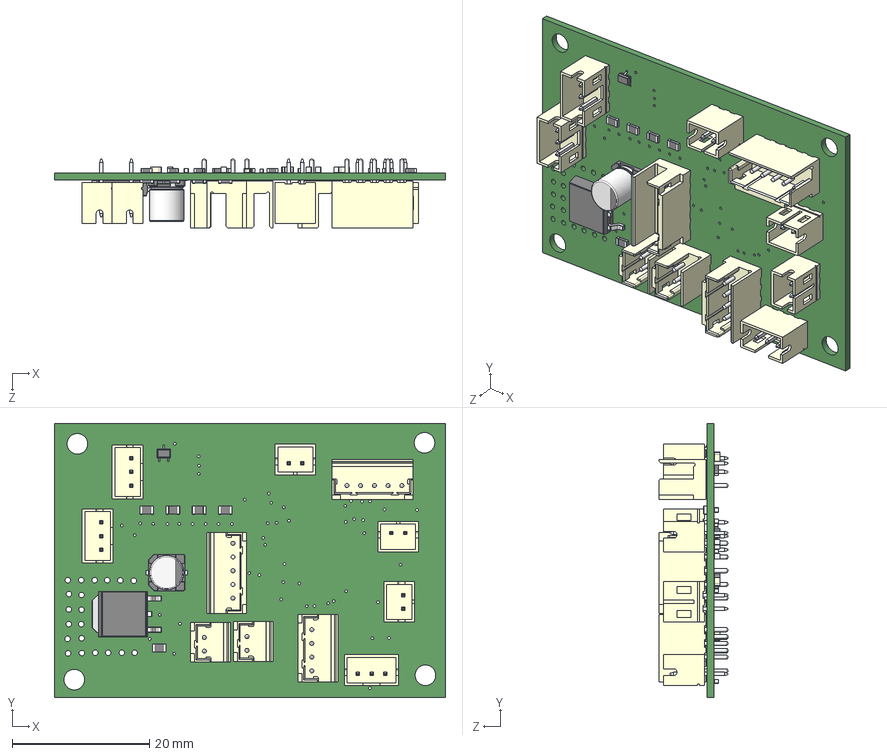
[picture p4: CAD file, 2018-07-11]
Projects/End effector/end_effector.step
57.0 x 40.0 x 10.0 mm
Board
cap_0402 x 2
cap_0603 x 11
capae-5.3x5.3h6.1
sot323
res_0805 x 5
hdr-1x3t_2_sh8x5 x 3
hdr-1x2t_2_sh6x6 x 2
hdr-1x2t_2_sh6x5 x 3
hdr-1x5t_2_sh12x6 x 2
hdr-1x4t_2_sh10x6
res_0603 x 14
to252-3(4)_10x6.6x2.28

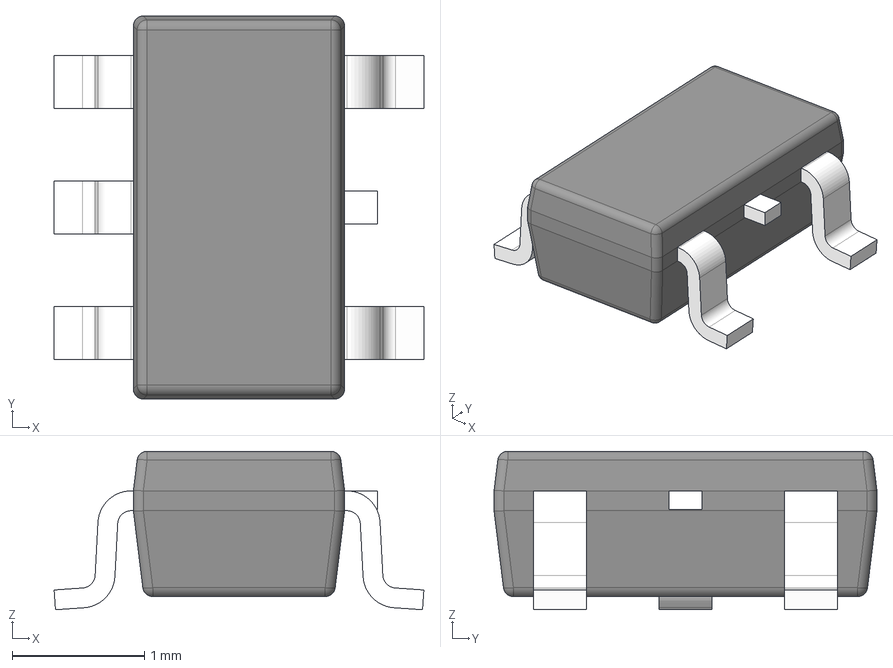
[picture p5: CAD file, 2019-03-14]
Projects/Motor controller/SN74AHC1G02DBVT.stp
2.80 x 2.90 x 1.20 mm
BODY-SOT
LEAD-SOT x 5
LEAD-DUMMY

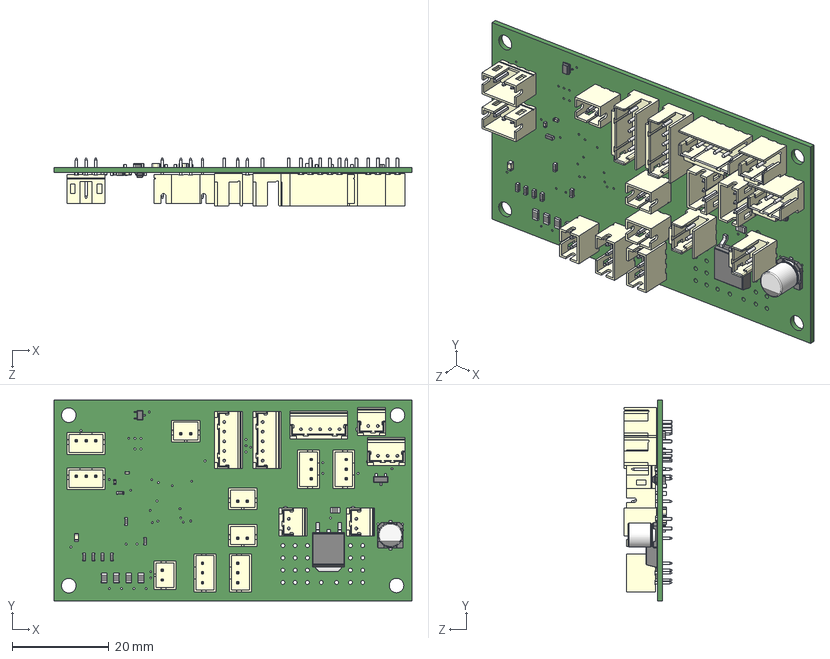
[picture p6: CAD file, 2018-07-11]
Projects/Science board/Science_board.step
74.0 x 41.5 x 10.0 mm
Board
cap_0603 x 11
cap_0402 x 2
capae-5.3x5.3h6.1
sot323
res_0805 x 5
hdr-1x2t_2_sh6x6 x 3
hdr-1x3t_2_sh8x5 x 6
hdr-1x2t_2_sh6x5 x 4
hdr-1x5t_2_sh12x6 x 3
hdr-1x3t_2_sh8x6
sot23
res_0603 x 19
to252-3(4)_10x6.6x2.28

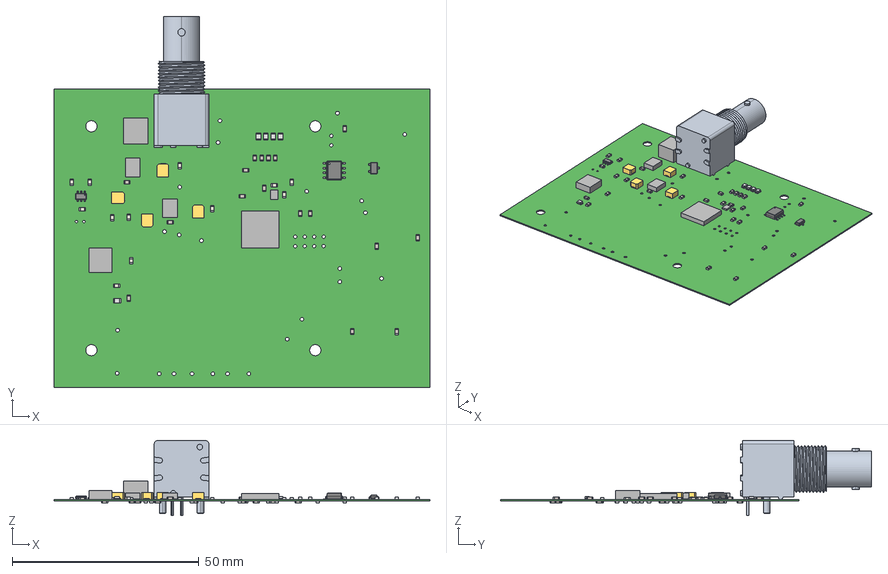
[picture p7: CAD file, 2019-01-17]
Projects/STEP files/Science.step
100.7 x 99.4 x 20.1 mm
Board
Extruded x 193
BODY_MK06A
LEAD_MK06A x 6
Open_CASCADE_STEP_translator_6.8_2.1
Open_CASCADE_STEP_translator_6.8_2.2.1
Leader x 11
c-1-1337543-0-e-3d
Open_CASCADE_STEP_translator_6.8_1.1.1

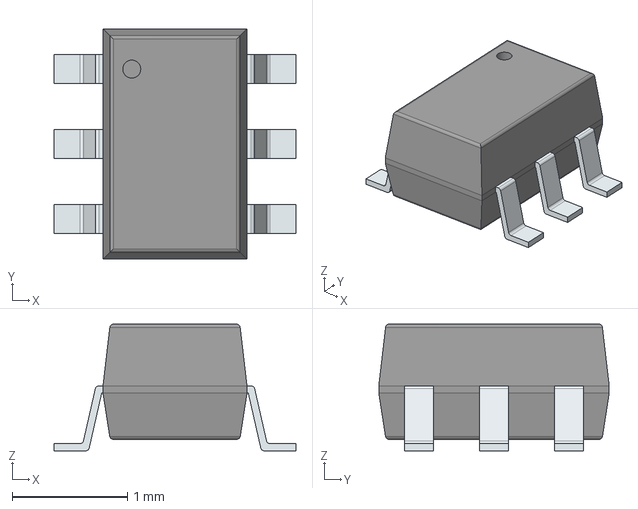
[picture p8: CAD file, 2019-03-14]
Projects/Motor controller/74LVC1G3157GW,125.stp
2.10 x 2.00 x 1.10 mm
PinsArrayLR

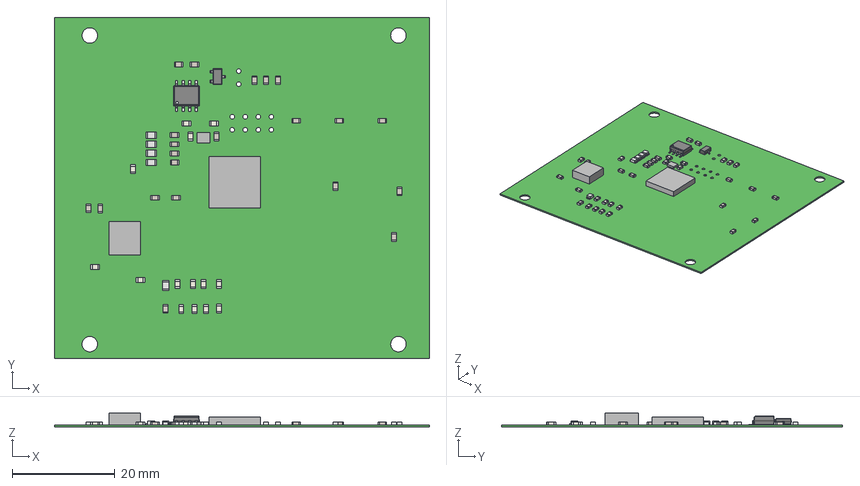
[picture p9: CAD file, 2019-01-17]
Projects/STEP files/Arm.step
72.9 x 66.3 x 2.79 mm
Board
Extruded x 118
Open_CASCADE_STEP_translator_6.8_2.1
Open_CASCADE_STEP_translator_6.8_2.2.1
Leader x 11
Open_CASCADE_STEP_translator_6.8_1.1.1

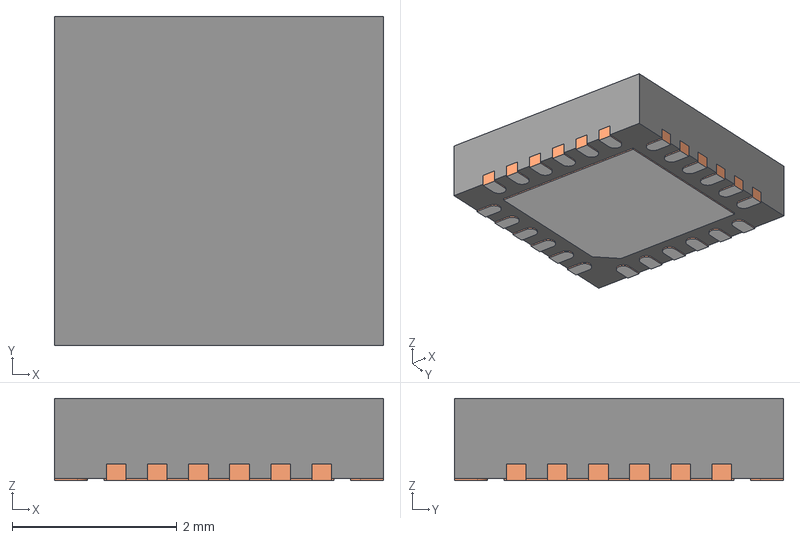
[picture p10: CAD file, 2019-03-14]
Projects/Motor controller/DRV8701.stp
4.00 x 4.00 x 1.00 mm
BODY-QFN
FRAME-RGE0024F
PIN1-ID

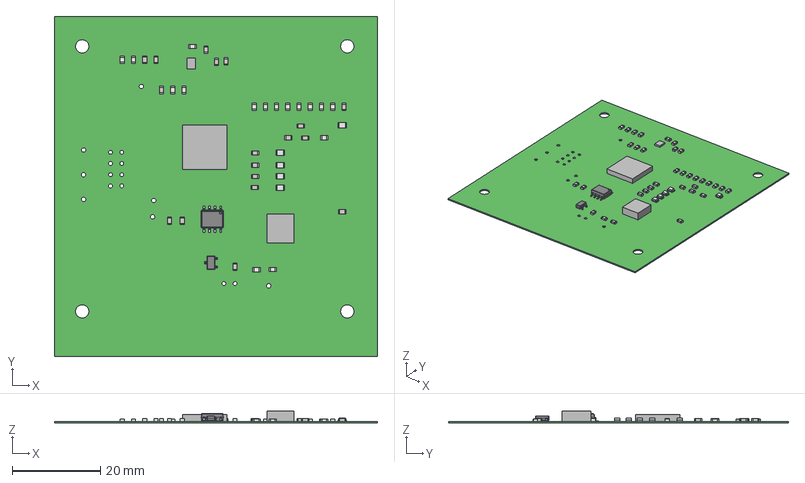
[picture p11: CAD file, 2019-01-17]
Projects/STEP files/Safety.step
73.2 x 77.0 x 2.79 mm
Board
Extruded x 115
Open_CASCADE_STEP_translator_6.8_2.1
Open_CASCADE_STEP_translator_6.8_2.2.1
Leader x 11
Open_CASCADE_STEP_translator_6.8_1.1.1

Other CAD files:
Projects/Arm board/armboard1_layout_12PINCONNECTOR.SLDPRT
Projects/End effector/end_effector.SLDPRT

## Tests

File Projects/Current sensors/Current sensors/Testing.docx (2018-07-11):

Determine if current sensor circuit resolves a linear relationship between current and voltage output by the op-amp. ADC’s not available. Used multimeter connected to op-amp Vout and Arduino ground with gator clips. Arduino UNO supplied 3V3 and 5V power. Used Agilent power supply to provide current. Soldered ~20 gauge wire to terminals of hall-effect sensor to attach supply to.

3v3 from UNO 30A

Current | Voltage (Measured twice Oct12) | Voltage(Oct 14)
0 | 3.22, 3.206 | 3.248
0.2 | 3.21, 3.198
0.4A (0.07V) | 3.205, 3.184 | 3.227
0.6 (.11 | 3.195, 3.175
00.8 (0.15 | 3.186,3.169
1(0.159 | 3.171,3.166 | 3.197
1.2 | 3.163,3.152
1.4 | 3.152,3.141
1.5 | | 3.172
1.6 | 3.145, 3.130
2 | __,3.107 | 3.147
2.5 | | 3.122
3 | | 3.092
3.5 | | 3.074
4 | | 3.050
4.5 | | 3.026
| | 3.002

5V supplied from arduino 30A

Current | voltage | Voltage oct 14
0A | 4.86, 4.84 | 4.87
0.2 | 4.83, 4.82
.4 | 4.81,4.80 | 4.84
.6 | 4.75, 4.78
.8 | 4.76, 4.77
1 | 4.76, 4.75 | 4.79
1.5 | 4.72,4.71 | 4.75
2 | 4.68,4 67 | 4.71
2.5 | ___,4.63 | 4.67
3 | | 4.63
3.5 | | 4.59
4 | | 4.55
4.5 | | 4.51/4.52 fluctuating
5 | | 4.47
6
7

From current sensor directly: 30A

Current | Vout (5V source)
0 | 2.5
0.5 | 2.533
1 | 2.567
1.5 | 2.598
2 | 2.629
2.5 | 2.661
3 | 2.693
3.5 | 2.726
4 | 2.765
4.5 | 2.798
5 | 2.829

F = (kq1q2)/r2

1N*r² =(kq1q2) =F(0.5r)²

F = 1/4N

After putting on new resistors for 5V supply

Current | voltage | Current Vout
0 | 1.150 | 2.5
.5 | 1.155 | 2.548
1 | 1.160 | 2.607
1.5 | 1.165 | 1.648
2 | 1.170 | 2.697
2.5 | | 2.745
3 | | 2.795
3.5 | | 2.8434
4 | 1.189 | 2.894
4.5 | | 2.954
5 | 1.198 | 2.993

October 28 3v3 20A board with new resistor values (potentially fried op amp)

Current | Vout (3V3 source)
0 | 1.638
| 1.659
1 | 1.681
| 1.701
2 | 1.722
| 1.743
3 | 1.764
| 1.785
4 | 1.807
| 1.828
5 | 1.850

-current to voltage out from sensor is linear and results are as expected 0.100V/A.

- voltage out from the op-amp was linear. But not as expected because the op amp was not inverting for some reason. Resistor values are correct.

30A Sensor board (potential fried op amp) Oct 28th

Current | Vout (op amp)
0 | 4.87
.5 | 4.83
1 | 4.79
1.5 | 4.75
2 | 4.71
2.5 | 4.68
3 | 4.64
3.5 | 4.60
4 | 4.56
4.5 | 4.52
5 | 4.48

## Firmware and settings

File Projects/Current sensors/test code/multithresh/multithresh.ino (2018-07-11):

     /*
     * This code is for an arduino connected to multiple custom current sensing boards via i2c
     * The program sampels the output from each of the boards using the i2c "wire" library and store it in an array "raw_adc" 
     * If a current drop is detected, the sensor data is then time stamped and send to a text file on a sd card module.
     * If no current drop is detected, then no data is saved. 
     *  
     *  
     */
    #include <Wire.h>
    #include <SD.h>
    #include <SPI.h>

    File myFile;
    int pinCS = 10; // Pin 10 on Arduino Uno
    int ADC_address[6]={ 0x52, 0x55,0x5A,0x50, 0x51, 0x54};
    // 0x59: 89    0x58: 88     0x51: 81    0x52: 82      0x56:86     //0x54:84(bad)   //0x5A:90
    int len = sizeof(ADC_address)/sizeof(ADC_address[0]);  //get array length
    float raw_adc[6];
    float current[6];
    float start_time=millis();
    int save =0;
    float thresh[6] ; 
    /*each board has its own current threshold. Anytime current draw of a board is below its thresh, data is saved.
    The thresh is set to the 50th current sample read from each individual board*/
    int run=1;

    
    void setup() { 
      
      Wire.begin(); //init i2c communication
      Serial.begin(9600);
      pinMode(pinCS, OUTPUT);
      
      // SD Card Initialization
      if (SD.begin()){
        Serial.println("SD card is ready to use.");
      } else{
        Serial.println("SD card initialization failed");
        return;
      }    
    }




    
    void loop() {
      delay(300);
      
      for (int i =0; i<len; i++){
          unsigned int data[2];     
          Wire.requestFrom(ADC_address[i], 2); //request 2 bytes of data
          
          if(Wire.available() == 2){
            data[0] = Wire.read();
            data[1] = Wire.read();
  }

          // Convert the data to 8 bits and calculate current
          raw_adc[i] = (((data[0] & 0x0F) * 256) + (data[1] & 0xF0)) / 16.0 ;  
          current[i]= float((245- raw_adc[i])/7.520); //VERIFIED FOR BOARDS 2 AND 3//robotics: changed from 241 to 245//maggie 7.52 for 5V, used 46 for 3v3


          //make the 50th current sample the threshold
          run=run+1;
          if (run>50 && run<56){
            
            Serial.print("----run reached------------");
            Serial.print("");
            thresh[i]=current[i];
            }

          //enter save mode if the threshold is passed
          if(((thresh[i] -current[i]) >0.1) ||(run>500 && run<506)){
            save=1;
            }

          Serial.print("raw adc "); 
          Serial.println(raw_adc[i]);
          Serial.print(ADC_address[i]);
     
          Serial.print(" current ->" );
          Serial.println( current[i]);

        }//for each data grabbing board // data acquisition

delay(500);


//----------------------------------------------
        
if (save==1){     
  // make a string for assembling the data to log:
  String dataString = "";

  // read all sensors and append to the string:
  for (int board = 0;  board< len; board++) {
    dataString += "Current:  " + String(current[board])+" Address: "+ String(ADC_address[board]);
    
    if (board < (len-1)) {
      dataString += ",";
      
    }
    else{
      float now =(millis()-start_time)/1000;
      dataString += ", Time :"+ String(now);
      save=0;
      } 
    }




  //-------------open file and save

  // open the file. note that only one file can be open at a time,
  // so you have to close this one before opening another.
  File dataFile = SD.open("datalog.csv", FILE_WRITE);

  // if the file is available, write to it:
  Serial.println("-------------------");
  if (dataFile) {
    dataFile.println(dataString);
    dataFile.close();
    // print to the serial port too:
    
    Serial.println(dataString);
  }
  // if the file isn't open, pop up an error:
  else {
    Serial.println("error opening datalog.txt");
  }
  Serial.println("-------------------");
  delay(500);
    }
    }//if

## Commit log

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2018-07-07 Added a line to motor controller bom, added both libraries, a schematic, and a pcb file
    [motor_controller_BOM.xlsx]
2018-07-11 Adding relevant files and folders from 2018 grabcad
    I'm keeping all the projects, we can delete it later if it's useless
    [100A bom.xlsx, 30A bom.xlsx, 3d model.step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]
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2018-11-14 Updated CAN schematic to include jumper (1x2 male pin header)
    [CAN.SchDoc]
2018-11-14 Update project file b/c of updated CAN sch
    [Template.PrjPCB]
2018-11-18 reorganised science board folders started science board Altium project
    [Science_board.step, Science_board.xlsx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]
2018-11-19 added reference documents for all the sensors started wiring up sensors in the schematics
    [can.SchDoc, connectors.SchDoc, mcu.SchDoc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]
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2018-11-20 Added motor signals. Started work on pH signal conditioning circuit. Added some schematic symbols.
    [Adafruit Flora TCS34725.brd, Adafruit Flora TCS34725.sch, Adafruit TCS34725.PrjPcb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]
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2018-11-21 Almost finished pH sheet and made schematic symbols as needed.
    [mcu.SchDoc, ph.SchDoc, science_board_proj_rev_1.PrjPcb]
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2018-11-23 More changes to schematic: Finished pH conditioning circuit Added oscillator and motor connectors Added a TODO file
    [Adafruit TCS34725.SchDoc, connectors.SchDoc, mcu.SchDoc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]
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2018-11-24 template fix
    [ArmPCBPrj.PrjPCB, CAN.SchDoc, Connectors.SchDoc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]
2018-11-25 Made a template folder for all template schematic/pcb
    [CAN.SchDoc, Connectors.SchDoc, MCU.SchDoc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]
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2018-11-25 Changes UART and SWD connectors to one 4x2 header
    [Connectors.SchDoc]
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2018-11-25 Puts both limit switches (for one motor) on one connector
    [Connectors.SchDoc]
2018-11-26 Added schematics for support. PWM pulldowns and limit switch pull ups. Added testpoints on a load of signals. Changed connectors for motor signals.
    [Support.SchDoc, connectors.SchDoc, mcu.SchDoc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]
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2018-11-26 Adds Power (Voltage regulator) to template, updates reference designators, adds a .33uF cap to the schematic library
    [Connectors.SchDoc, MCU.SchDoc, POWER.SchDoc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]
2018-11-27 Adds power, changes the micro to have passive inputs (to avoid Altium errors), removes net names (redundant since we are using ports), updated reference designators
    [CAN.SchDoc, Connectors.SchDoc, MCU.SchDoc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]
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2018-11-28 changed motor pins to fit guidelines, encoders still WIP
    [mcu.SchDoc]
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2018-11-29 changed net port names to match the ones on the MC
    [connectors.SchDoc]
2018-11-29 added LEDs to support schematic, minor refining of net names
    [connectors.SchDoc, mcu.SchDoc, support.SchDoc]
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2018-12-28 Removed 'resources' folder in Science project
    reason: Filenames were too long and causing update issues
    [Adafruit Flora TCS34725.brd, Adafruit Flora TCS34725.sch, Adafruit TCS34725.brd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]
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2019-01-04 Adds footprint for CAN transceiver, adds 0603 resistor (to replace 0201)
2019-01-04 Fixes footprint for 22uF capacitor, updates resistor footprint sizes, adds footprint to CAN transceiver, adds Header (for terminating CAN resistors) to library
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2019-01-05 Moved safety board 2018 into a separtae folder
    [BoardOutline.gbr, Bottom.gbr, BottomAssy.gbr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]
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2019-01-06 added some parameters to the schlib, tried compiling the science board
    [science_board_2019.PcbDoc]
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2019-01-07 added footprint for polarised 10uF cap, started PCB document
    [can.SchDoc, connectors.SchDoc, mcu.SchDoc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]
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2019-01-09 finished routing pH circuit, started layout on connectors
    [can.SchDoc, connectors.SchDoc, mcu.SchDoc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]
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2019-01-09 Adds 260k resistor to library, updates temperature sensor on safety board
    [CAN.SchDoc, Connectors.SchDoc, MCU.SchDoc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]
2019-01-09 Adds resitors to libraries, adds power redundancy to safety board
    [Connectors.SchDoc, MCU.SchDoc, POWER.SchDoc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]
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2019-01-12 fixed designators on connectors and testpoints
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2019-01-12 avoided a nightmare, routed most of the science board
    [Connectors.SchDoc, MCU.SchDoc, POWER.SchDoc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]
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2019-01-13 Pushing more or less finished schematic, altium is dumb
    [74LVC1G3157GW_125.PcbLib, 74LVC1G3157GW_125.SchLib, DRV8701PRGET.PcbLib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]
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2019-01-13 Updated schematics to include terminals and sourced 10mOhm resistor
    [OTHERTEST.PrjPcb, OTHERTEST_0.SchDoc, OTHERTEST_1.SchDoc]
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2019-01-13 added a 2nd CAN connector, PWM testpoints and changed the LED
    [can.SchDoc, connectors.SchDoc, mcu.SchDoc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]
2019-01-13 narrowly avoided a panic attack, ran DRC on PCB
    [science_board_pcb.PcbDoc]
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2019-01-13 added board name, rev, and my name on the silkscreen
    [science_board_pcb.PcbDoc]
2019-01-14 Modified thermal relief so copper pour underneath is also 3v3
    [science_board_pcb.PcbDoc]
2019-01-14 Updated library components, added proper thermal relief to 3V3 voltage regulator
    [ArmPCBPrj.PrjPCB]
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2019-01-14 Fixed regulator area, fixed some missing connections
    [Safety_rev1.PcbDoc]
2019-01-14 Switched R16 and R15 because of inconsistency. Replaced C14 and C13 with appropriate cap values
    [ArmPCB.PcbDoc, POWER.SchDoc, Support.SchDoc]
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2019-01-14 Fixed some clearance issues
    [ArmPCB.PcbDoc]
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2019-01-17 updates design item ids on tespoint and connectors to prevent overwriting of comments
    [Arm.step, ArmPCB.PcbDoc, ArmRev2.PcbDoc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]
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2019-01-18 changed CAN footprint, reverted resistors
    [can.SchDoc, connectors.SchDoc, mcu.SchDoc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]
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2019-01-18 Safety Board Updated
    - capacitors hopefully fixed
    - voltage divider resistances changed to account for a factor of safety (30V instead of 24V)
    - LTC2875 footprint updated
    [CAN.SchDoc, POWER.SchDoc, Safety_rev1.PcbDoc]
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2019-01-18 Added trace to connect 3v3 to voltage divider, removed text that said to update caps
    [Safety_rev1.PcbDoc]
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2019-01-18 Revert "Merge branch 'master' of https://github.com/uwrobotics/MarsRover2019-PCB"
    This reverts commit 410cfb74c72f63003ee715a044fd58b441a3355f, reversing
    changes made to 72b2dded087129662167543ed7c96ce859771808.
    [ArmRev2.PcbDoc, Connectors.SchDoc]
2019-01-18 fixed issue with 3v3 net on arm board revision
    [ArmPCBPrj.PrjPCB, ArmRev2.PcbDoc, CAN.SchDoc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]
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2019-01-19 Modified connector names to be more descriptive, hid their designators. Expanded ground for C14. Increased track size of 3V3 in some areas.
    [ArmRev2.PcbDoc, CAN.SchDoc, Connectors.SchDoc]
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2019-01-19 Added keep out layer, modified 3v3 track to fit with new keep out layer
    [science_board_pcb.PcbDoc]
2019-01-19 Fixed missing trace, added keep out layer.
    [Safety_rev1.PcbDoc]
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2019-01-20 Added footprints for motor controller board to library and connected to schematic
    [OTHERTEST.PrjPcb, OTHERTEST_0.SchDoc, OTHERTEST_1.SchDoc]
2019-01-28 added a load of output files, including PDF versions of the schematics
    [Bill of Materials-science_board_proj_rev_1.xlsx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]
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2019-02-11 Deleted not needed schematics, replaced ressister values, changed test points formats based on schematics review feedback
    [can.SchDoc, mcu.SchDoc, power.SchDoc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]
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2019-02-17 component error fix
    [BOM_motor_controller.xlsx, buy_components.xlsx]
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2019-02-18 Updated library with proper motor controller components, modified schematics to correct logic
    [MCMainSch.SchDoc, MC_Sch2.SchDoc, Motor Controller V2.PrjPCB]
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2019-02-28 Updated TVS diode with correct footprint, modified 10uF caps to correct footprints
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2019-03-04 Fixed a right angle route on Gimbal board
    [Gimbal19_V1.PcbDoc]
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2019-03-11 - Changed ENC pin to Ftf pin in case it swings >3V - Waived component clearance violations
    [Gimbal19.PrjPcb, Gimbal19_V1.PcbDoc, mcu.SchDoc]
2019-03-11 Fixed DRV component to include pin "25" (large GND pad)
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2019-03-11 Updated DRV footprint to correct one, there are errors now, but because of the capacitor placed underneath.
    [MCMainSch.SchDoc, MC_PCB.PcbDoc, Motor Controller V2.PrjPCB]
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2019-03-17 Changed C14 to polarized symbol so we don't confuse the polarity of the tantalum cap. Also increase the size of the ground plane for C14 and regulator.
    [power.SchDoc, science_board_pcb.PcbDoc]
2019-03-17 Changed footprints of 10uF capacitor to avoid confusion. We shouldn't mix up polarized and non-polarized caps
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2019-03-28 Updated BOM and Schematic
    Coordinated with Robbie to find unknown capacitances and resistances, updated schematic and BOM for the 100A current sensor.
    [BOM - Current Sensor v7.4.xlsx]
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2019-03-30 Fixed some missing connections and shrank board down a bit.
    [science_board_pcb.PcbDoc]
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2019-03-30 Modified footprint library, increased size of vias on VQFN Modified motor controller schematic so that AVDD and DVDD is connected to pins on chip. Thickened some of the traces on PCB.
    [MCMainSch.SchDoc, MC_PCB.PcbDoc, MC_Sch2.SchDoc]
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2019-04-06 Fixed PWM and DIR trace so it's all on the top layer to maximize GND plane on bottom. Increased trace width of Vbat2 net from bulk cap.
    [MC_PCB.PcbDoc]
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
